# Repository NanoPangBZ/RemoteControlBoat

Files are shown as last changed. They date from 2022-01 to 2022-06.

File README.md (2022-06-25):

# 2022年机创项目(已结束)

## 1、硬件说明(机械创新实验室成员使用船只演示时必看!!!)

	船核心板与船驱动板之间的信号线连接采用MX1.25（4Pin 8Pin都有），虽然驱动板上忘记写标志了，对齐了连接即可。驱动板P3口是给核心板供电（5V）的，核心板的P2、P4是3.3V电源，千万别接5V，不然直接GG!!

    模块接口主要包括MPU6050、nRF24L01和七脚OLED12864，具体连接自己研究吧，这个应该简单。

    **本次比赛中电机等的连接**

    因为船核心板的单片机使用的是自己老项目的拆机芯片，TIM4CH1的出波有些问题，使用PWM模式能出波，但是这个管脚的PWM峰值远远低于3.3V,无法使用这个信号驱动舵机电调等，所以硬件上没有连接！

    因为这个原因，原定使用 TIM4 CH1~CH4 做为电调控制的引脚 **改为** TIM8 CH1~CH4。(注意：驱动板上TIM8口标的是舵机驱动舵机接口，但是软件上并没有使用TIM8控制舵机，而是使用TIM8控制电调。TIM4的CH1和CH4没有使用,CH2和CH3用于控制舵机。)

	主推进无刷电机使用电调控制，电调分别连接TIM8的CH1和CH2，这种电调和其他电调的区别是它用的香蕉头！不要搞错了，另一种电调用来驱动转向电机的，它无法提供主推进无刷电机的电流!!然后主推进电机的电调是可调油门的双向电调，我已经油门行程校准过了，建议看不懂程序就别瞎校准油门行程了！！转向无刷电机的电调它是不可调行程的电调，没有油门行程校准的功能(使用TIM8的CH3和CH4)。

	**遥控器**

	没啥好讲的，Type-C接口有根线忘记连接了，电脑无法识别到CH340就把Type-C翻一面连接。

## 2、软件说明

	自己看代码注释去，懒得BBNN。没学RTOS也能看，底层分的很清除的。

	**boat工程:**

	bsp_pwm.c/.h -> 船核心板输出PWM

	bsp_spi.c/.h -> SPI通讯 用于2.4G通讯模块 和 OLED屏幕 (注意:没有初始化代码)

	bsp_usart.c/.h -> 串口,部分使用的DMA发送,自己看

	bsp_timer.c/.h -> 代码计时器，可用于计算某些代码的运行时长

## 3、写在最后

	没必要老是跟着船走，你可以自己设计一块其它功能的驱动板，调用我的底层去控制其它东西，霍尔啊啥的。驱动板注意做好隔离，别把核心板烧了！！那块板子上的单片机是我自己的！！！！！

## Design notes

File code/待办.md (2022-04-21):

测试遥控器屏幕是否会显示nrf断连消息

购买XT60和香蕉头口

购买水位检测器

购买图传

搭建最终硬件

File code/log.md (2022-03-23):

freeRTOS下通过一个任务函数使用不同的任务参数建立多个任务:

错误示范:



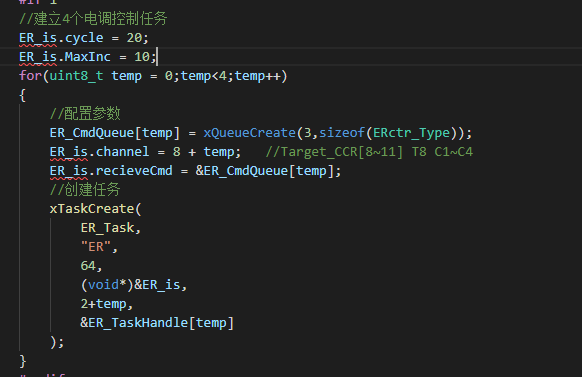
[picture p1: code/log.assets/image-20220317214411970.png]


ER_is->任务参数,函数内定义的局部变量

不能使用同一ER_Type变量建立多个任务,因为TaskCreate函数传入的是地址!相当于多个任务使用了同一个参数

Pass:



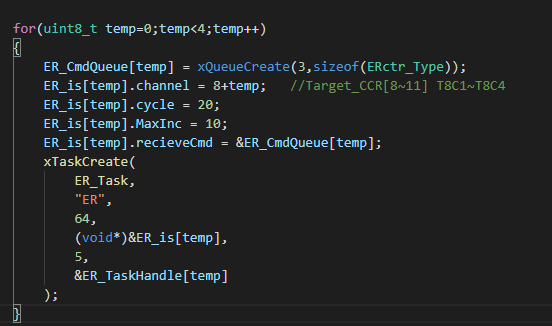
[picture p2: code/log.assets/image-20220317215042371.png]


```c
#include "stdui.g"

void main(void)
{
    
}
```

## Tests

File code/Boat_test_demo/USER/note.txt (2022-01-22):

待办:
    nRF24L01 进入ISR正常
    nRF24L01移植
    6路PWM输出
说明:
-主控芯片待定! 6路PWM(4路50Hz,2路10kHz)、2路PWM捕获、2路ADC采集、1路4Pin-SPI(nRF24L01)、1串口、软件I2C(陀螺仪)
-nrf24l01：只使用P0和P1数据管道。P0用于发送模式下接收ACK信号，P1用于接收模式下接收数据。P0的地址与发射模式下
 发射地址保持一致(发送端P0地址、发送端发射地址和接收端P1地址三者一致)。遥控器发射地址"USER"(5Byte)，P1管道地
 址"BOAT"(5Byte)，船控制器与遥控器相反。

便签:

备注: 2022年机创，水面清洁机器人 船控制器

最后更改日期:2021年1月 庞碧璋 3096470072@qq.com

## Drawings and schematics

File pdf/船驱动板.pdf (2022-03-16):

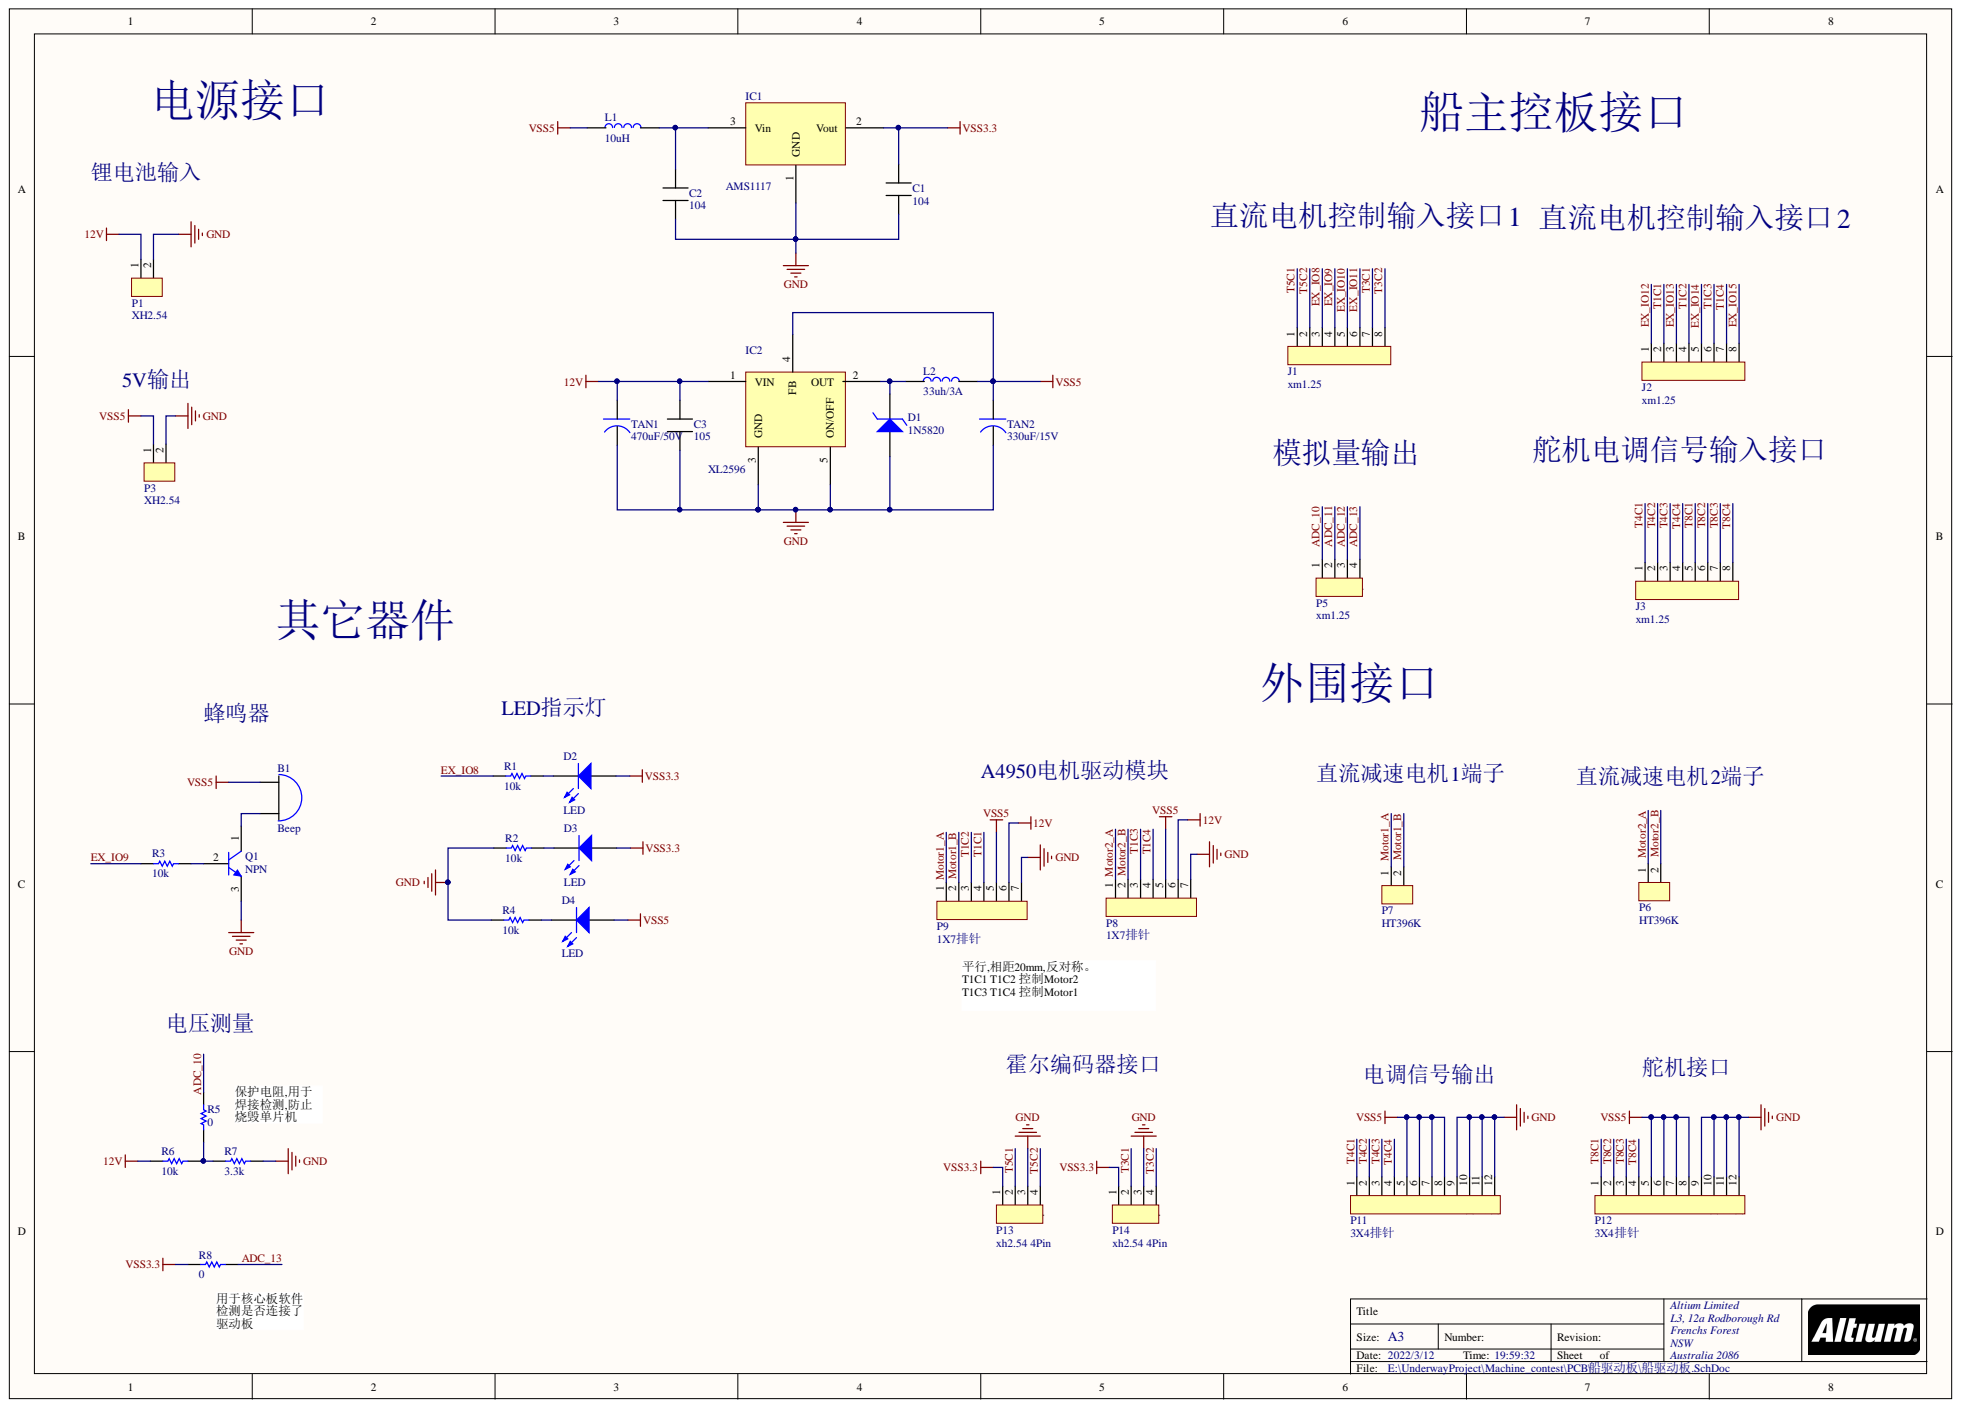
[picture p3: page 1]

Comment | Description | Designator | Footprint | LibRef | Quantity
Beep | | B1 | 蜂鸣器 | Beep | 1
104 | | C1 | C 0603 | 电容 | 1
104 | | C2 | C 0603 | 电容 | 1
105 | | C3 | C 0603 | 电容 | 1
1N5820 | | D1 | 1N5824 | 稳压二极管 | 1
LED | Typical INFRARED GaAs LED D2 | | LED 0603 | LED | 1
LED | Typical INFRARED GaAs LED D3 | | LED 0603 | LED | 1
LED | Typical INFRARED GaAs LED D4 | | LED 0603 | LED | 1
AMS1117 | | IC1 | SOT-223 | AMS1117-3.3 | 1
XL2596 | | IC2 | TO-263-5 | XL2596 | 1
xm1.25 | | J1 | MX1.25 8P LS | 1X8排针 | 1
xm1.25 | | J2 | MX1.25 8P LS | 1X8排针 | 1
xm1.25 | | J3 | MX1.25 8P LS | 1X8排针 | 1
10uH | | L1 | L 0603 | 电感 | 1
33uh/3A | | L2 | CDRH74 | 电感 | 1
XH2.54 | | P1 | XH2.54 2P | 1X2排针 | 1
XH2.54 | | P3 | XH2.54 2P | 1X2排针 | 1
xm1.25 | | P5 | MX1.25 | 1X4排针 | 1
HT396K | | P6 | HT396 - 2P | 1X2排针 | 1
HT396K | | P7 | HT396 - 2P | 1X2排针 | 1
1X7排针 | | P8 | 2.54 1X7Pin | 1X7排针 | 1
1X7排针 | | P9 | 2.54 1X7Pin | 1X7排针 | 1
3X4排针 | | P11 | 2.54 3X4 | 3X4排针 | 1
3X4排针 | | P12 | 2.54 3X4 | 3X4排针 | 1
xh2.54 4Pin | | P13 | XH2.54 -4p | 1X4排针 | 1
xh2.54 4Pin | | P14 | XH2.54 -4p | 1X4排针 | 1
NPN | NPN Bipolar Transistor Q1 | | SOT-23 | NPN | 1
10k | Resistor | R1 | R 0603 | Res | 1
10k | Resistor | R2 | R 0603 | Res | 1
10k | Resistor | R3 | R 0603 | Res | 1
10k | Resistor | R4 | R 0603 | Res | 1
0 | Resistor | R5 | R 0603 | Res | 1
10k | Resistor | R6 | R 0603 | Res | 1
3.3k | Resistor | R7 | R 0603 | Res | 1
0 | Resistor | R8 | R 0603 | Res | 1
470uF/50V | | TAN1 | 10X10.5mm 电解电容极性电容 | | 1
330uF/15V | | TAN2 | 8*10.0mm 电解电容极性电容 | | 1

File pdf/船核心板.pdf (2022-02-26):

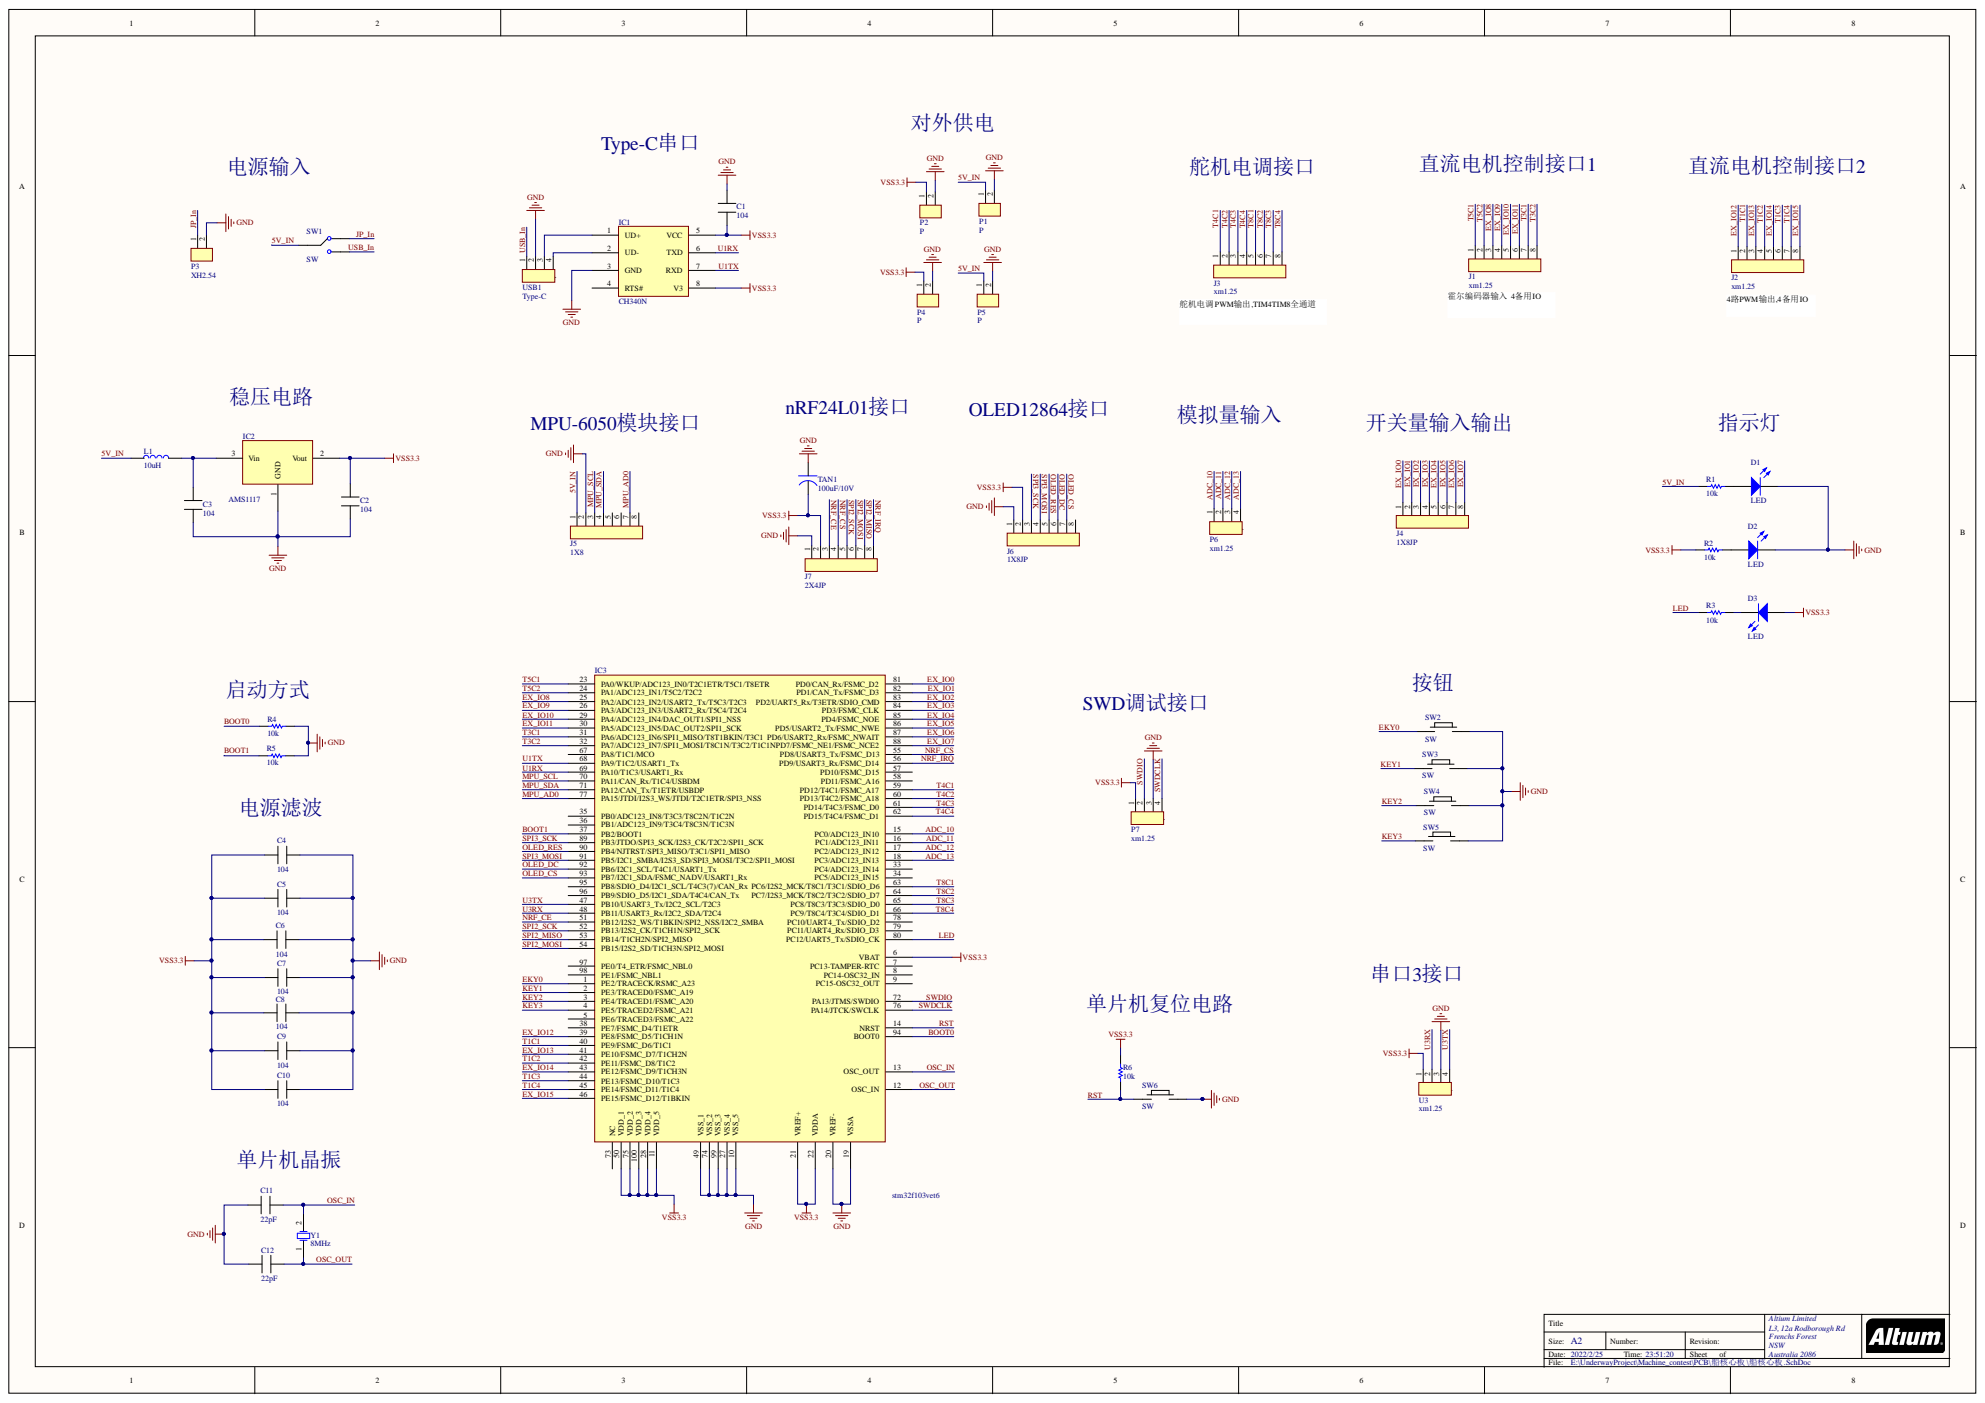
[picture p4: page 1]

GND 3

RTS# 4

Title | Altium Limited L3, 12a Rodborough Rd Frenchs Forest NSW Australia 2086

Size: A2 | Number: | Revision:

Date: 2022/2/25 Time: 23:51:20 | | Sheet of

E:\UnderwayProject\Machine_contest\PCB\船核心板\船核心板.SchDoc

Comment | Description | Designator | Footprint | LibRef | Quantity
104 | | C1, C2, C3, C4, C5, C6, C7, C8, C9, C10 C 0603 | | 电容 | 10
22pF | | C11, C12 | C 0603 | 电容 | 2
LED | Typical INFRARED GaAs LED D1, D2, D3 | | LED 0603 | LED | 3
CH340N | | IC1 | SOP-8 | CH340N | 1
AMS1117 | | IC2 | SOT-223 | AMS1117-3.3 | 1
stm32f103vet6 | | IC3 | LQPF100 12X12 | stm32f103vet6 | 1
xm1.25 | | J1, J2, J3 | MX1.25 8P | 1X8排针 | 3
1X8JP | | J4, J6 | HDR2.54-M-LI-8P | 1X8排针 | 2
1X8 | | J5 | HDR2.54-M-LI-8P | 1X8排针 | 1
2X4JP | | J7 | HDR2.54-LI-2x4P | 1X8排针 | 1
10uH | | L1 | L 0603 | 电感 | 1
P | | P1, P2, P4, P5 | XH2.54 2P | 1X2排针 | 4
XH2.54 | | P3 | XH2.54 2P | 1X2排针 | 1
xm1.25 | | P6, P7 | MX1.25 | 1X4排针 | 2
10k | Resistor | R1, R2, R3, R4, R5, R6R 0603 | | Res | 6
SW | | SW1 | 拨动开关 9X3.5X3.5 侧卧 单刀双置开关 | | 1
SW | | SW2, SW3, SW4, SW5, SW6 SW SMD 3x6x2.5 | | 弹簧开关 | 5
100uF/10V | | TAN1 | 6.3*5.4mm 电解电容极性电容 | | 1
xm1.25 | | U3 | 2.54 _ 4Pin | 1X4排针 | 1
Type-C | | USB1 | USB Type-C | 1X4排针 | 1
8MHz | Crystal Oscillator | Y1 | OSC SMD | 晶振 | 1

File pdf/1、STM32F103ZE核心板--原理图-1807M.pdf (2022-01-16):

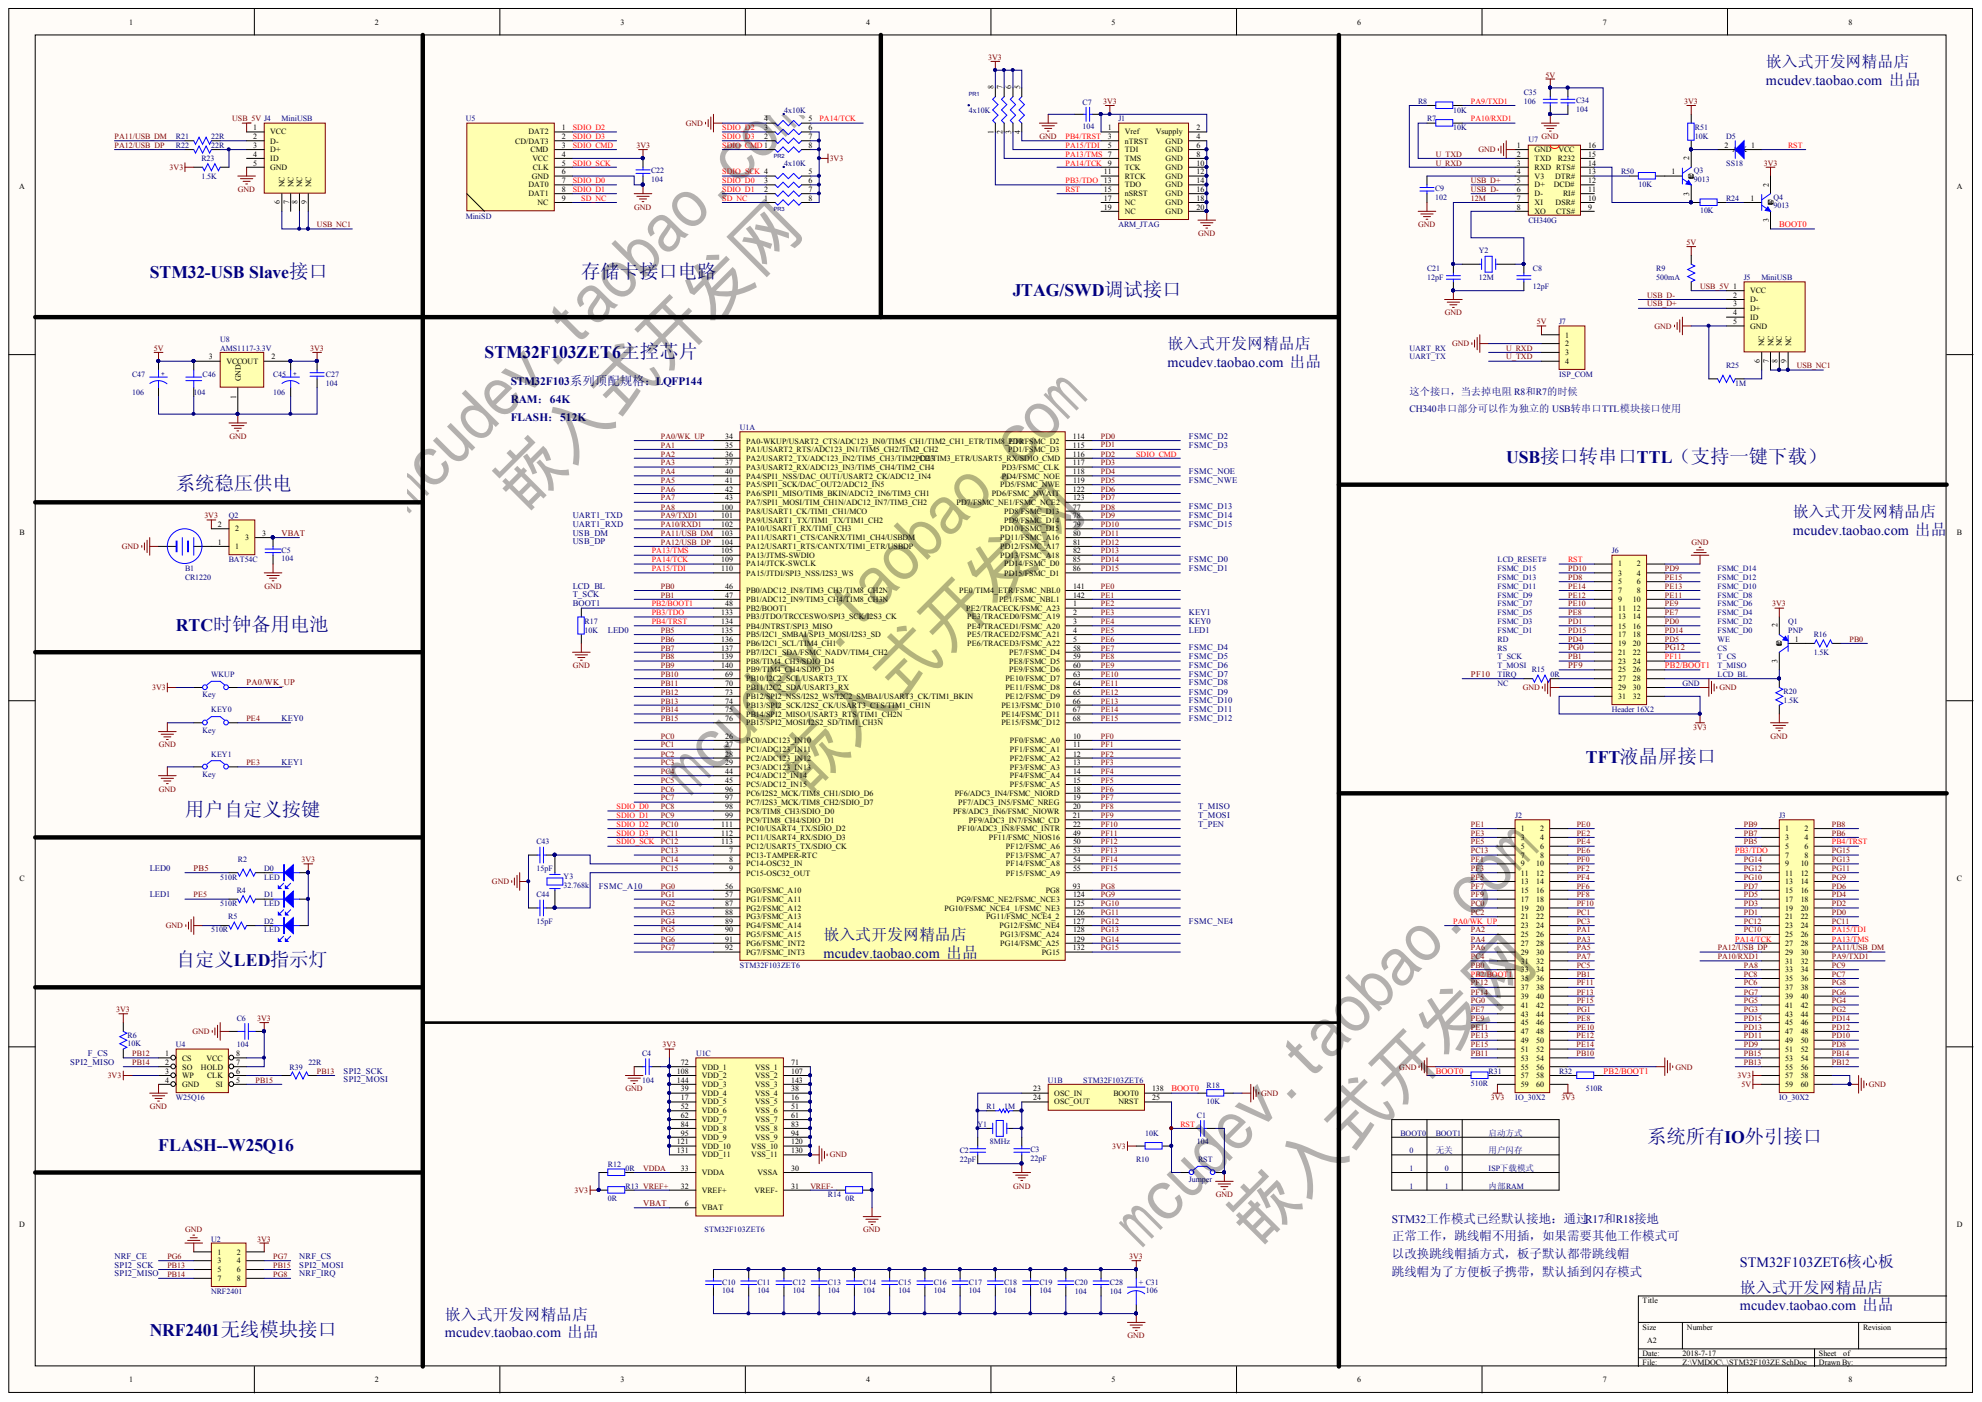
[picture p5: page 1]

STM32F103ZET6核心板 mcudev.taobao.com 出品

嵌入式开发网精品店
mcudev.taobao.com 出品

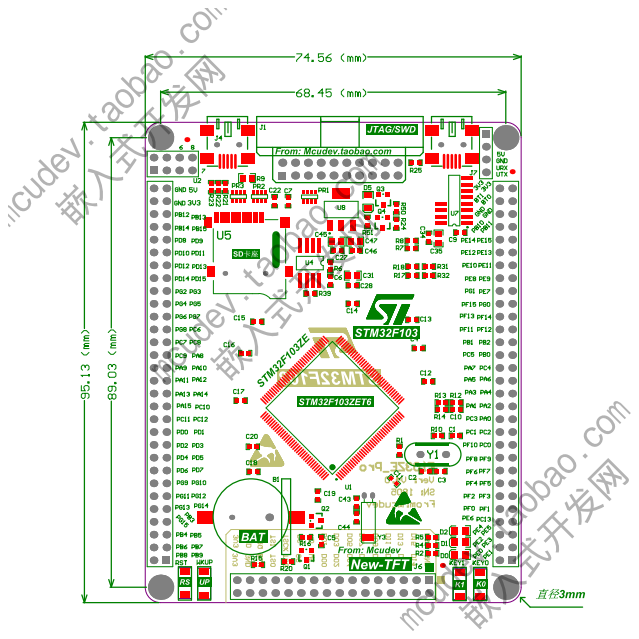
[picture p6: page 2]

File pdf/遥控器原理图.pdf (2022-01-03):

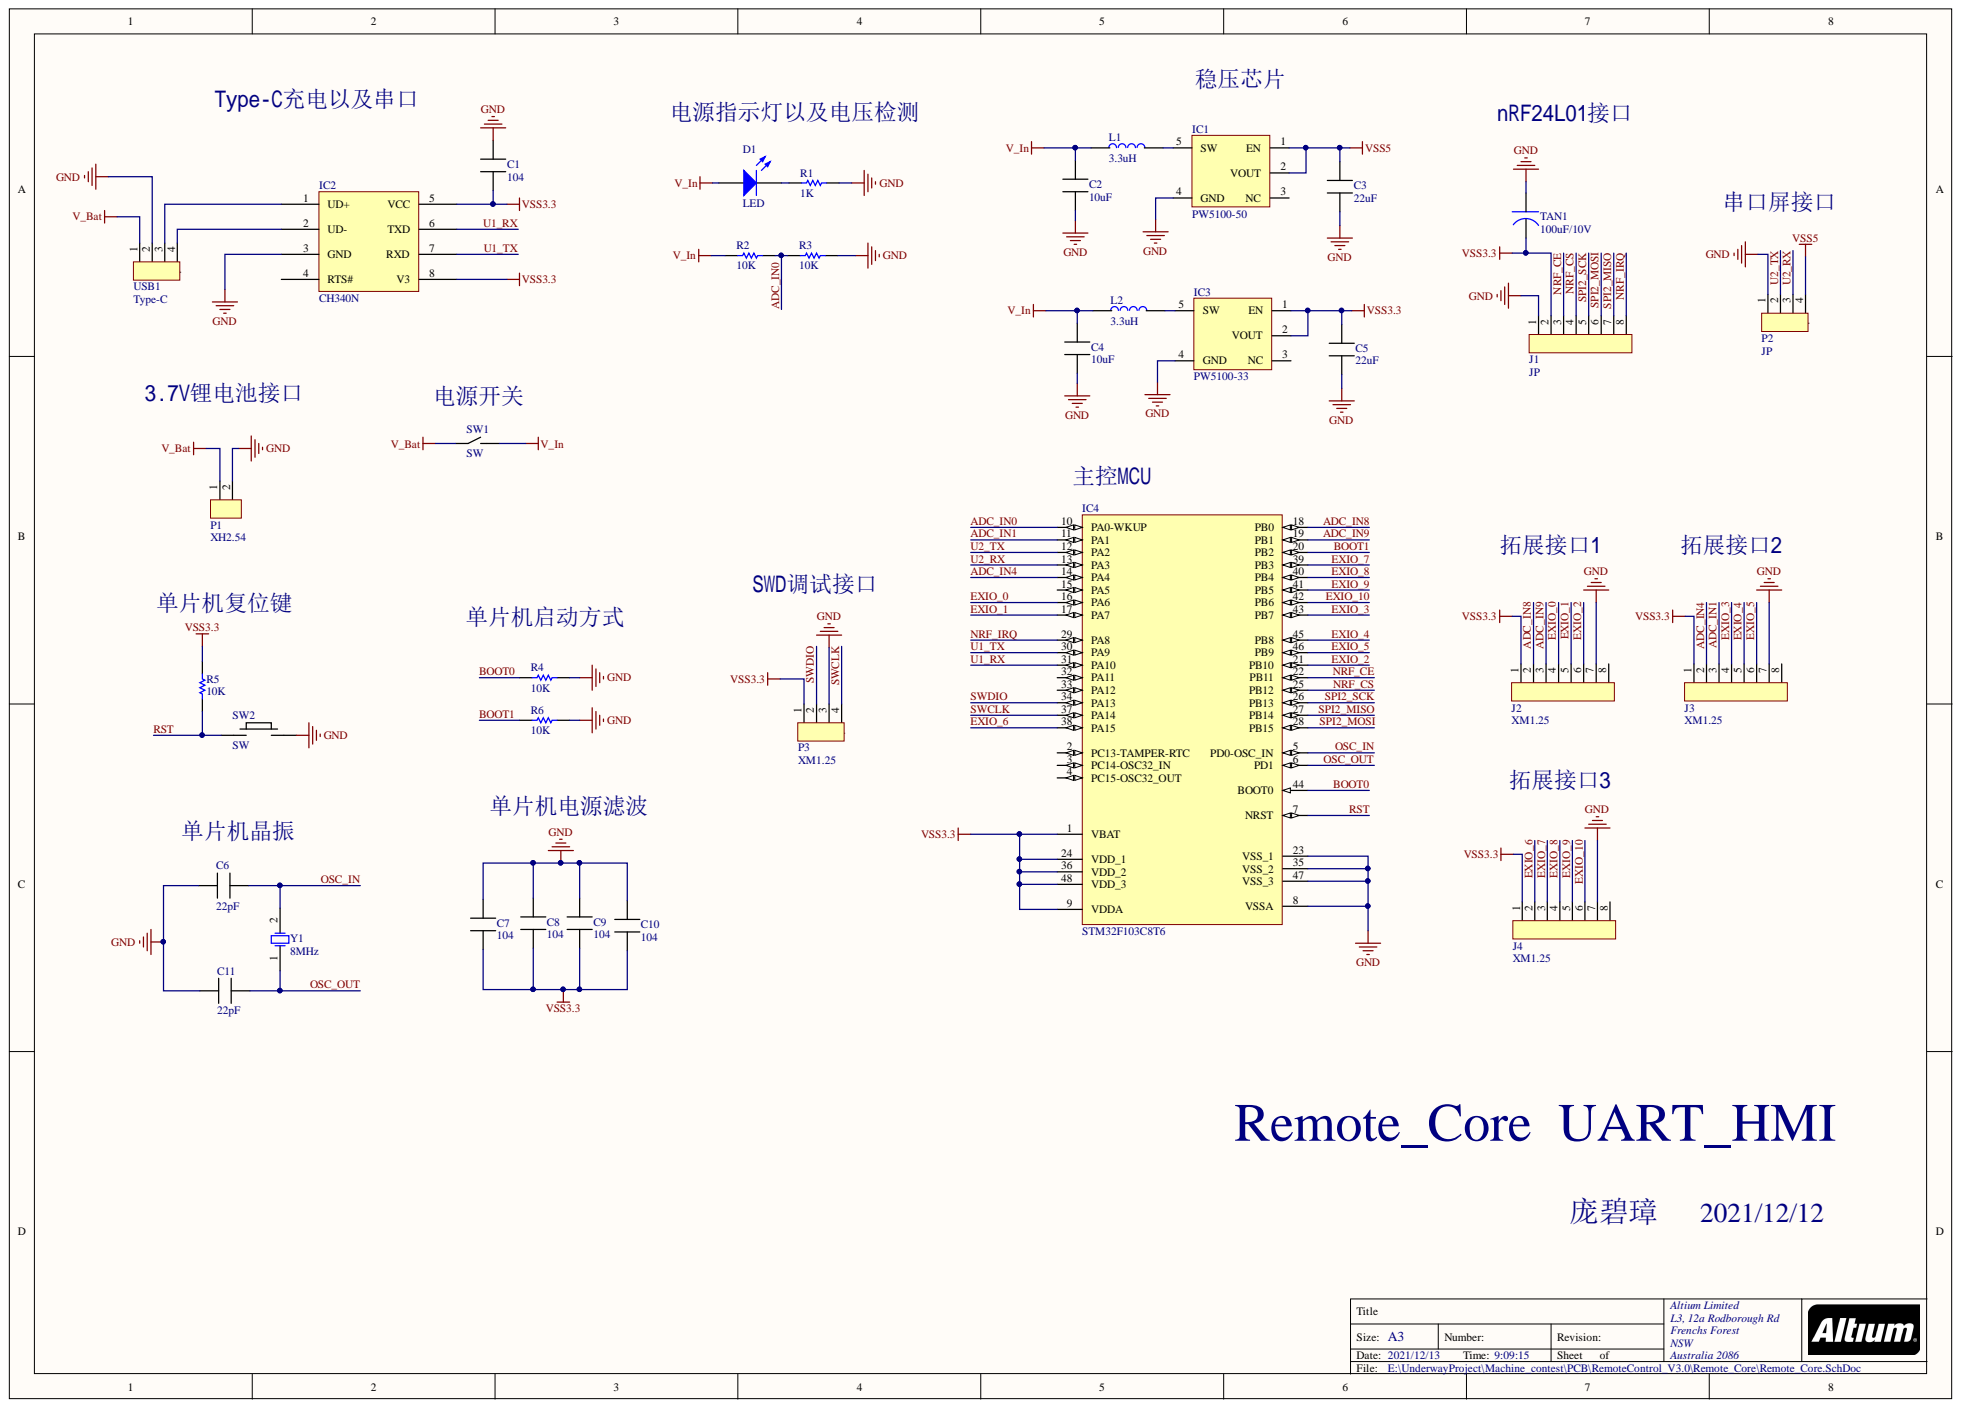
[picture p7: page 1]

Ti t l e | A l t ium Li m i ted L3, 12a Rodborough R d F renchs Fores t NSW Aus t ral ia 2086

Size: A 3 | Number : | Revi s ion:
Date: 2021/12/13 Ti me: 9:09:15 | | Sheet of

Comment | Description | Designator | Footprint | LibRef | Quantity
104 | | C1 | C 0603 | 电容 | 1
10uF | | C2 | C 0603 | 电容 | 1
22uF | | C3 | C 0603 | 电容 | 1
10uF | | C4 | C 0603 | 电容 | 1
22uF | | C5 | C 0603 | 电容 | 1
22pF | | C6 | C 0603 | 电容 | 1
104 | | C7 | C 0603 | 电容 | 1
104 | | C8 | C 0603 | 电容 | 1
104 | | C9 | C 0603 | 电容 | 1
104 | | C10 | C 0603 | 电容 | 1
22pF | | C11 | C 0603 | 电容 | 1
LED | Typical INFRARED GaAs LED D1 | | LED 0603 | LED | 1
PW5100-50 | | IC1 | PW5100 | PW5100 | 1
CH340N | | IC2 | SOP-8 | CH340N | 1
PW5100-33 | | IC3 | PW5100 | PW5100 | 1
STM32F103C8T6 | | IC4 | LQPF48 7X7 | stm32f103c8t6 | 1
JP | | J1 | HDR2.54-LI-2x4P | 1X8排针 | 1
XM1.25 | | J2 | MX1.25 8P | 1X8排针 | 1
XM1.25 | | J3 | MX1.25 8P | 1X8排针 | 1
XM1.25 | | J4 | MX1.25 8P | 1X8排针 | 1
3.3uH | | L1 | 630 | 电感 | 1
3.3uH | | L2 | 630 | 电感 | 1
XH2.54 | | P1 | XH2.54 2P | 1X2排针 | 1
JP | | P2 | 2.54 _ 4Pin | 1X4排针 | 1
XM1.25 | | P3 | MX1.25 | 1X4排针 | 1
1K | Resistor | R1 | R 0603 | Res | 1
10K | Resistor | R2 | R 0603 | Res | 1
10K | Resistor | R3 | R 0603 | Res | 1
10K | Resistor | R4 | R 0603 | Res | 1
10K | Resistor | R5 | R 0603 | Res | 1
10K | Resistor | R6 | R 0603 | Res | 1
SW | | SW1 | 拨动开关 9X3.5X3.5 侧卧 开关 | | 1
SW | | SW2 | SW SMD 3x6x2.5 | 弹簧开关 | 1
100uF/10V | | TAN1 | 6.3*5.4mm 电解电容极性电容 | | 1
Type-C | | USB1 | USB Type-C | 1X4排针 | 1
8MHz | Crystal Oscillator | Y1 | OSC SMD | 晶振 | 1

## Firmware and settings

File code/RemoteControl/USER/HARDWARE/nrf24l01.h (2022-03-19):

#ifndef _NRF24L01_H_
#define _NRF24L01_H_

#include "self_stm32f10x.h"

/*************************************************
 * nrf24l01的驱动
 * nrf24l01.c
 * nrf24l01.h
 * nrf24l01_micro.h <- nrf寄存器地址
 * 
 * 功能:
 * 驱动nrf24l01 1对1 半双工通讯 (只支持静态接收字节长度,长度可配置)
 * 可使用文件内部的sbuffer来缓存多次接收(可通过宏配置)
 * 
 * 若宏NRF24_USE_SBUFFER==1,nRF24L01_InterruptHandle()会
 * 将nrf RxFIFO中的值读入到nRF24L01_Sbuffer中
 * 若宏NRF24_USE_BUF_LEN==0,则nRF24L01_Sbuffer会被下次接收时
 * 调用nRF24L01_InterruptHandle()覆盖
 * 
 * 关于移植:
 * 
 * 实现nrf24l01.c中的宏和nrf_support_init()
 * 注意!nrf的中断服务函数没有写接口,可以在外部
 * 的中断函数中调用nRF24L01_InterruptHandle()
 * 
 * 如果是接收中断可能会耗费较长的时序,不建议直接
 * 在中断服务函数中调用nRF24L01_InterruptHandle()
 * 
 * 如果不想使用外部中断,可以不在nrf_support_init()
 * 中配置中断,轮询nRF24L01_InterruptHandle()即可
 * 
 * 作者: 庞碧璋
 * Github: https://github.com/CodingBugStd
 * csdn:   https://blog.csdn.net/RampagePBZ
 * Encoding: utf-8
 * 最后更改时间: 2022/2/14
*************************************************/

/*************************自定义宏**********************************/
// spi_port
#define  NRF24L01_SPIx                SPI2                  // SPI 端口   

// 第3脚:CE
#define  NRF24L01_CE_GPIO             GPIOB                 // CE 工作模式开启， 高电平有效，发射/接收模式控制
#define  NRF24L01_CE_PIN              GPIO_Pin_11
// 第4脚:CSN
#define  NRF24L01_CSN_GPIO            GPIOB                 // SPI 软件片选线
#define  NRF24L01_CSN_PIN             GPIO_Pin_12
// 第5脚:SCK
#define  NRF24L01_SCK_GPIO            GPIOB                 // SPI SCK
#define  NRF24L01_SCK_PIN             GPIO_Pin_13
// 第65脚:MOSI
#define  NRF24L01_MOSI_GPIO           GPIOB                 // SPI MOSI
#define  NRF24L01_MOSI_PIN            GPIO_Pin_15
// 第7脚:MISO
#define  NRF24L01_MISO_GPIO           GPIOB                 // SPI MISO
#define  NRF24L01_MISO_PIN            GPIO_Pin_14
// 第8脚:IRQ
#define  NRF24L01_IQR_GPIO           GPIOA                 // SPI IRQ
#define  NRF24L01_IQR_PIN            GPIO_Pin_8
#define  NRF24L01_IQR_Channel        EXTI9_5_IRQn
#define  NRF24L01_IQR_SourceGPIO    GPIO_PortSourceGPIOA
#define  NRF24L01_IQR_PinSource     GPIO_PinSource8
#define  NRF24L01_IQR_Line          EXTI_Line8

#define NRF24L01_CE     0
#define NRF24L01_CS     1
#define NRF24L01_MOSI   2
#define NRF24L01_MISO   3
#define NRF24L01_SCK    4

/*************************************功能配置宏************************************************/

//相关配置
//nRF24初始化的默认配置
#define DEFAULT_TxAddr  "USER"
#define DEFAULT_RxAddr  "BOAT"
#define DEFAULT_Channel 0       //2400MHz频段
#define DEFAULT_RETRY   2       //最大自动重发次数
#define DEFAULT_RETRY_CYCLE 1   //重发间隔 单位:250us
#define DEFAULT_Rx_Length   32  //默认StaticPayload长度
//其它配置
#define NRF24_BUF_MAXLEN    64  //缓存区长度,NRF24_USE_BUF_LEN!=0 时才有用
#define NRF24_USE_BUF_LEN   0   //非0:缓存区第一字节用于表示缓存区长度,使能这个宏可以缓存nrf24的多次接收
#define NRF24_USE_SBUFFER   1   //非0:接收中断时将RxFIFO的值载入内部缓存nRF24L01_Sbuffer中,若NRF24_USE_BUF_LEN=0则会覆盖上次接收!

#if NRF24_USE_BUF_LEN
//缓存区第一字节表示缓存区当前长度
static uint8_t nRF24L01_Sbuffer[NRF24_BUF_MAXLEN+1] = {0};
#elif NRF24_USE_SBUFFER
static uint8_t nRF24L01_Sbuffer[32] = {0};
#endif

typedef struct
{
    uint8_t Channel;    //频道  0~125 -> 1MHz + 2.4G
    uint8_t retry;      //自动重发次数 最大16
    uint8_t retry_cycle;//自动重发时间间隔 250us单位 最大16(4000us)
    uint8_t Rx_Length;  //静态接收长度
    uint8_t RX_Addr[5]; //接收地址    ->  发射方地址
    uint8_t TX_Addr[5]; //发射方地址  ->  目标接收地址
}nRF24L01_Cfg;

static nRF24L01_Cfg CurrentCfg;     //当前nRF24L01的配置

/*************************************函数************************************************/

//底层函数

uint8_t nRF24L01_Send_Cmd(uint8_t cmd);
uint8_t nRF24L01_Send_CmdAndData(uint8_t cmd,uint8_t*buf,uint8_t len);
uint8_t nRF24L01_Read_Reg(uint8_t addr);
uint8_t nRF24L01_Read_Buf(uint8_t addr,uint8_t*buf,uint8_t len);
uint8_t nRF24L01_Write_Reg(uint8_t addr,uint8_t dat);
uint8_t nRF24L01_Write_Buf(uint8_t addr,uint8_t*buf,uint8_t len);

//用户函数

uint8_t nRF24L01_Init(void);
uint8_t nRF24L01_Check(void);
uint8_t nRF24L01_Status(void);
uint8_t nRF24L01_Config(nRF24L01_Cfg*Cfg);
uint8_t nRF24L01_Send(uint8_t*buf,uint8_t len);
uint8_t nRF24L01_Read_RxFIFO(uint8_t*buf);
uint8_t nRF24L01_Rx_Mode(void);
#if NRF24_USE_SBUFFER
uint8_t nRF24L01_Read_RxSbuffer(uint8_t*buf,uint8_t len);
uint8_t*nRF24L01_Get_RxBufAddr(void);
uint8_t*nRF24L01_FIFO_To_Sbuffer(void);
#if NRF24_USE_BUF_LEN
uint8_t nRF24L01_Read_SbufferLen(void);
void nRF24L01_Push_Sbuffer(uint8_t len);
void nRF24L01_Clear_Sbuffer(void);
#endif  //NRF24_USE_BUF_LEN
#endif //NRF24_USE_SBUFFER

void nRF24L01_InterruptHandle(void);
void Rx_Handler(void);   //接收中断
void NoACK_Handle(void); //未应答中断
void Tx_Handle(void);    //发送完成中断

#endif

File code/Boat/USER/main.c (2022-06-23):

#include "main.h"

#pragma	diag_suppress	870	//屏蔽汉字警告

//nRF24L01初始化结构体
nRF24L01_Cfg nRF24_Cfg;
static uint8_t RxAddr[5] = {0x43,0x16,'R','C',0xFF};	//遥控器地址
static uint8_t TxAddr[5] = {0x43,0x16,'B','T',0xFF};	//船地址

//任务参数
uint8_t main_fre = 50;				//主任务频率
uint8_t oled_fre = 20;				//OLED刷新频率
uint8_t WaterLine_fre = 50;			//水位测量频率
uint8_t nrf_maxDelay = 200;			//nrf最大超时时间
uint8_t mpu_fre = DEFAULT_MPU_HZ;	//mpu更新频率
ER_Type	ER_is[4];					//电调任务参数
DCMotor_Type DCMotor_is[2];			//直流电机任务参数
StreetMotor_Type STMotor_is[3];		//舵机任务参数

//任务句柄
TaskHandle_t	RTOSCreateTask_TaskHandle = NULL;	//创建任务句柄
TaskHandle_t	ReplyMaster_TaskHandle = NULL;		//主机回复任务句柄
TaskHandle_t	OLED_TaskHandle = NULL;				//oled刷新任务句柄
TaskHandle_t	nRF24L01_Intterrupt_TaskHandle = NULL;	//nrf中断任务句柄
TaskHandle_t	MPU_TaskHandle = NULL;				//陀螺仪刷新任务句柄
TaskHandle_t	KeyInput_TaskHandle = NULL;			//按键任务句柄
TaskHandle_t	Voltage_TaskHandle = NULL;			//电池电压检测任务句柄
TaskHandle_t	DepthSensor_TaskHandle = NULL;		//水位深度检测任务句柄
TaskHandle_t	Beep_TaskHandle = NULL;				//蜂鸣器任务句柄
TaskHandle_t	ER_TaskHandle[4] = {NULL,NULL,NULL,NULL};	//电调任务句柄
TaskHandle_t	DCMotor_TaskHandle[2] = {NULL,NULL};		//直流电机控制任务句柄
TaskHandle_t	StreetMotor_TaskHandle[4] = {NULL,NULL,NULL,NULL};	//舵机任务句柄

//队列句柄
SemaphoreHandle_t	nRF24_ISRFlag = NULL;		//nrf24硬件中断标志
SemaphoreHandle_t	nRF24_RecieveFlag = NULL;	//nrf24接收标志(数据已经进入单片机,等待处理)
QueueHandle_t		nRF24_SendResult = NULL;	//nrf24发送结果
QueueHandle_t		wait_handle_receive = NULL;	//等待处理的接收信息
QueueHandle_t		ER_CmdQueue[4] = {NULL,NULL,NULL,NULL};	//电调任务命令接收队列
QueueHandle_t		DCMotor_CmdQueue[2] = {NULL,NULL};		//直流电机任务命令接收队列
QueueHandle_t		STMotor_CmdQueue[4] = {NULL,NULL,NULL,NULL};	//舵机任务命令接收队列
QueueHandle_t		Beep_CmdQueue = NULL;		//蜂鸣器命令队列
SemaphoreHandle_t	mpuDat_occFlag = NULL;		//mpu数据占用标志(互斥信号量)
SemaphoreHandle_t	sysStatus_occFlag = NULL;	//系统状态变量占用标志(互斥信号量)

//全局变量
float mpu_data[3] = {0,0,0};    //姿态 -> mpuDat_occFlag保护
float BatVol = 0.0f;			//电池电压
float Depth = 0.0f;				//吃水深度
sysStatus_Type sysStatus;       //系统状态 -> sysStatus_occFlag保护
PID_Handle	Yaw_pid_Handle;		//航向角pid

void RTOSCreateTask_Task(void*ptr);		//初始化任务
void Er_Cal(void);	//油门行程校准

int main(void)
{
	uint8_t nrf_err;
	uint8_t mpu_err;

	NVIC_PriorityGroupConfig(NVIC_PriorityGroup_4);
	//关闭JATG调试接口,开启SWD调试接口
	RCC_APB2PeriphClockCmd(RCC_APB2Periph_AFIO,ENABLE);
	GPIO_PinRemapConfig(GPIO_Remap_SWJ_JTAGDisable,ENABLE);

	BSP_PWM_Init();
	BSP_LED_Init();
	BSP_Usart_Init();
	//BSP_Timer_Init();
	BSP_Key_Init();
	BSP_Beep_Init();
	BSP_ADC_Init();
	BSP_i2c_Init();

	//OLED初始化 -> 需要SPI
	OLED12864_Init();
	OLED12864_Show_String(0,0,"hardware init",1);
	OLED12864_Refresh();


	Er_Cal();	//油门行程校准

	//MPU初始化	-> 需要IIC
	mpu_err = MPU_Init();
	if(mpu_err)
	{
		OLED12864_Show_String(2,0,"mpu err",1);
	}else
	{
		OLED12864_Show_String(2,0,"mpu pass",1);
		if(mpu_dmp_init())	//初始化官方的DMP固件库
			OLED12864_Show_String(3,0,"6050 dmp err",1);
	}

	//nrf24初始化和配置 -> 需要SPI
	nrf_err = nRF24L01_Init();
	if(nrf_err)	//检查硬件
	{
		OLED12864_Show_String(1,0,"nrf err.restarting",1);
		OLED12864_Refresh();
		while(nrf_err == 1)
		{
			nrf_err = nRF24L01_Init();
			soft_delay_ms(100);
		}
	}

	//nRF24L01 相关配置
	nRF24_Cfg.Channel = 50;	//2.45GHz 通讯频段
	nRF24_Cfg.retry = 10;	//最大重发次数
	nRF24_Cfg.retry_cycle = 1;	//重发周期
	nRF24_Cfg.Rx_Length = 32;	//结束长度
	MemCopy(TxAddr,nRF24_Cfg.TX_Addr,5);
	MemCopy(RxAddr,nRF24_Cfg.RX_Addr,5);
	nRF24L01_Config(&nRF24_Cfg);	//配置nRF24L01
	nRF24L01_Rx_Mode();

	OLED12864_Clear_Page(1);
	OLED12864_Show_String(1,0,"nrf pass",1);
	OLED12864_Refresh();

	//创建RTOS初始化任务
	if(nrf_err == 0 & mpu_err == 0)
	{
		xTaskCreate(
			RTOSCreateTask_Task,
			"init",
			256,
			NULL,
			15,
			&RTOSCreateTask_TaskHandle
		);
	}

	vTaskStartScheduler();

	while(1);
}

void RTOSCreateTask_Task(void*ptr)
{
	//系统状态sysStatus
    sysStatus.nrf_signal = 0;
	//建立 队列 信号量
    nRF24_ISRFlag = xSemaphoreCreateBinary();		//nrf外部中断标志,由isr给出
	nRF24_RecieveFlag = xSemaphoreCreateBinary();	//nrf发生接收中断标志
	nRF24_SendResult = xQueueCreate(1,1);			//nrf发送结果标志
    mpuDat_occFlag = xSemaphoreCreateMutex();		//mpu_data[3] 保护
    sysStatus_occFlag = xSemaphoreCreateMutex();	//sysStatus 保护
	Beep_CmdQueue = xQueueCreate(3,sizeof(BeepCtr_Type));
	//建立2个舵机控制任务
	STMotor_CmdQueue[0] = xQueueCreate(3,sizeof(StreetMotorCtr_Type));
	STMotor_is[0].queueAddr = &STMotor_CmdQueue[0];
	STMotor_is[0].streetMotor = streetMotor[0];	//见hardware_def.h
	STMotor_is[0].cycle = 40;	//25Hz执行频率
	STMotor_is[0].angle_inc = 4.7f;
	xTaskCreate(
		StreetMotor_Task,
		"SM",
		72,
		(void*)&STMotor_is[0],
		6,
		&StreetMotor_TaskHandle[0]
	);
	STMotor_CmdQueue[1] = xQueueCreate(3,sizeof(StreetMotorCtr_Type));
	STMotor_is[1].queueAddr = &STMotor_CmdQueue[1];
	STMotor_is[1].streetMotor = streetMotor[1];	//见hardware_def.h
	STMotor_is[1].cycle = 40;	//25Hz执行频率
	STMotor_is[1].angle_inc = 7.0;
	xTaskCreate(
		StreetMotor_Task,
		"SM",
		
		72,
		(void*)&STMotor_is[1],
		6,
		&StreetMotor_TaskHandle[1]
	);
	//建立2个直流电机控制任务
	for(uint8_t temp=0;temp<2;temp++)
	{
		DCMotor_CmdQueue[temp] = xQueueCreate(3,sizeof(DCMotorCtr_Type));	//创建命令接收队列
		DCMotor_is[temp].queueAddr = &DCMotor_CmdQueue[temp];				//设置命令接收队列地址
		DCMotor_is[temp].cycle = 20;	//50Hz执行频率
		DCMotor_is[temp].max_inc = 10;
		DCMotor_is[temp].a4950 = a4950[temp];	//见hardware_def.h
		xTaskCreate(
			Motor_Task,
			"MT",
			64,
			(void*)&DCMotor_is[temp],
			5,
			&DCMotor_TaskHandle[temp]
		);
	}
	//建立4个电调控制任务
	for(uint8_t temp=0;temp<4;temp++)
	{
		ER_CmdQueue[temp] = xQueueCreate(3,sizeof(ERctr_Type));		//创建命令接收队列
		ER_is[temp].queueAddr = &ER_CmdQueue[temp];					//设置命令接收队列地址
		ER_is[temp].er = er[temp];	//见hardware_def.h
		ER_is[temp].cycle = 20;
		ER_is[temp].max_inc = 20;
		xTaskCreate(
        	ER_Task,
        	"ER",
        	72,
        	(void*)&ER_is[temp],
        	5,
        	&ER_TaskHandle[temp]
    	);
	}
	#if 1
	//建立nrf回复主机任务
    xTaskCreate(
        ReplyMaster_Task,
        "Reply",
        256,
        (void*)&nrf_maxDelay,
        11,
        &ReplyMaster_TaskHandle
    );
	#endif
	//建立陀螺仪任务
    xTaskCreate(
        MPU_Task,
        "mpu",
        256,
        (void*)&mpu_fre,
        10,
        &MPU_TaskHandle
    );
	#if 1
	//建立oled显示任务
    xTaskCreate(
        OLED_Task,
        "oled",
        256,
        (void*)&oled_fre,
        8,
        &OLED_TaskHandle
    );
	#endif
	//建立nrf中断处理任务
    xTaskCreate(
        nRF24L01_Intterrupt_Task,
        "nrf interrupt",
        128,
        NULL,
        14,
        &nRF24L01_Intterrupt_TaskHandle
    );
	//建立水位检测任务
    xTaskCreate(
        DepthSensor_Task,
        "depth",
        48,
        &WaterLine_fre,
        9,
        &Voltage_TaskHandle
    );
	//建立电池电压检测任务
    xTaskCreate(
        Voltage_Task,
        "batvol",
        48,
        NULL,
        3,
        &Voltage_TaskHandle
    );
	//建立按键输入任务
    xTaskCreate(
        KeyInput_Task,
        "key",
        64,
        NULL,
        7,
        &KeyInput_TaskHandle
    );
	//建立蜂鸣器任务
	xTaskCreate(
		Beep_Task,
		"Beep",
		48,
		NULL,
		2,
		&Beep_TaskHandle
	);
	//鸣响,表示开始运行
	Beep_ON(Mu_Fre[4]);
	soft_delay_ms(800);
	Beep_OFF();
	//删除自身
    vTaskDelete(NULL);
}

//油门校准
void Er_Cal(void)
{
	//油门行程校准
	if(Key_Read(0) == Key_Press)
	{
		OLED12864_Show_String(0,0,"calibration",1);
		OLED12864_Refresh();
		soft_delay_ms(2000);
		ER_UndirOut(&er[0],0);
		ER_UndirOut(&er[1],0);
		ER_UndirOut(&er[2],0);
		ER_UndirOut(&er[3],0);
		while(Key_Read(0) != Key_Press);
		OLED12864_Show_String(1,0,"Set Max",1);
		OLED12864_Refresh();
		ER_UndirOut(&er[0],500);
		ER_UndirOut(&er[1],500);
		ER_UndirOut(&er[2],500);
		ER_UndirOut(&er[3],500);
		soft_delay_ms(300);
		while(Key_Read(0) != Key_Press);
		OLED12864_Show_String(1,0,"Set Med",1);
		OLED12864_Refresh();
		ER_UndirOut(&er[0],0);
		ER_UndirOut(&er[1],0);
		ER_UndirOut(&er[2],0);
		ER_UndirOut(&er[3],0);
		soft_delay_ms(300);
	}
}

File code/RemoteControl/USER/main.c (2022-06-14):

#include "main.h"

#pragma	diag_suppress	870	//屏蔽汉字警告

//nRF24L01初始化结构体
nRF24L01_Cfg nRF24_Cfg;
static uint8_t TxAddr[5] = {0x43,0x16,'R','C',0xFF};	//遥控器地址
static uint8_t RxAddr[5] = {0x43,0x16,'B','T',0xFF};	//船地址

//任务参数
uint8_t SendFre = 50;	//nrf24通讯频率
uint8_t RockerFre = 25;	//摇杆采样频率
uint8_t HMI_Fre = 24;	//串口屏幕刷新频率
uint8_t Key_Fre = 10;	//按钮扫描频率

//任务句柄
TaskHandle_t RTOS_CreatTask_TaskHandle = NULL;
TaskHandle_t RemoteControl_TaskHandle = NULL;
TaskHandle_t nRF24L01_Intterrupt_TaskHandle = NULL;
TaskHandle_t User_FeedBack_TaskHandle = NULL;
TaskHandle_t Rocker_TaskHandle = NULL;
TaskHandle_t HMI_TaskHandle = NULL;
TaskHandle_t KeyInput_TaskHandle = NULL;
TaskHandle_t HMI_UpDataHandle = NULL;

//队列句柄
SemaphoreHandle_t	nRF24_ISRFlag = NULL;		//nrf24硬件中断标志
SemaphoreHandle_t	nRF24_RecieveFlag = NULL;	//nrf24接收标志(数据已经进入单片机,等待处理)
QueueHandle_t		nRF24_SendResult = NULL;	//nrf24发送结果
SemaphoreHandle_t	boatGyroscope_occFlag = NULL;		//船只姿态数据占用标志(互斥信号量)

//全局变量
uint8_t nrf_signal = 0;		//nrf信号强度 0~10
float Depth = 0.0f;			//深度 单位cm
float BoatGyroscope[3];			//船只返回的姿态 boatGyroscope_occFlag保护
float BoatVoltage;
uint8_t rockerInput[4];			//摇杆输入
uint8_t SwitchValue = 0;	//开关量 8开关

void RTOS_CreatTask_Task(void*ptr);

int main(void)
{
	uint8_t nrf_err;

	//中断优先级分组 4位主优先级 0位子优先级
	NVIC_PriorityGroupConfig(NVIC_PriorityGroup_4);
	//关闭JTAG调试接口
	RCC_APB2PeriphClockCmd(RCC_APB2Periph_AFIO,ENABLE);
	GPIO_PinRemapConfig(GPIO_Remap_SWJ_JTAGDisable,ENABLE);

	//串口初始化
	BSP_Usart_Init();
	BSP_ADC_Init();	//ADC初始化
	BSP_LED_Init();
	BSP_Key_Init();

	//串口屏初始化
	soft_delay_ms(500);
	//串口屏开机要一段时间
	//为了串口屏能完整的接收到复位数据
	//初始化两次
	HMI_Reset();
	HMI_Reset();
	soft_delay_ms(500);

	//nRF24L01初始化
	nrf_err = nRF24L01_Init();
	if(nrf_err)
	{
		HMI_Msg("nrf err");
	}else
	{
		//nRF24L01 相关配置
		nRF24_Cfg.Channel = 50;	//2.45GHz 通讯频段
		nRF24_Cfg.retry = 10;	//最大重发次数
		nRF24_Cfg.retry_cycle = 1;	//重发周期
		nRF24_Cfg.Rx_Length = 32;	//结束长度
		MemCopy(TxAddr,nRF24_Cfg.TX_Addr,5);
		MemCopy(RxAddr,nRF24_Cfg.RX_Addr,5);
		nRF24L01_Config(&nRF24_Cfg);	//配置nRF24L01	
		HMI_Msg("nrf pass");
		nRF24L01_Rx_Mode();
	}

	soft_delay_ms(1000);

	xTaskCreate(
		RTOS_CreatTask_Task,
		"CreatTask",
		144,
		NULL,
		15,
		&RTOS_CreatTask_TaskHandle
	);

	vTaskStartScheduler();
	while(1);
}

void RTOS_CreatTask_Task(void*ptr)
{
    nRF24_ISRFlag = xSemaphoreCreateBinary();		//创建nrf中断信号量 -> 由单片机(硬件)外部中断给出
	nRF24_RecieveFlag = xSemaphoreCreateBinary();	//创建nrf接收中断信号量 -> 由(软件)nrf中断处理函数给出
	nRF24_SendResult = xQueueCreate(1,1);			//创建nrf发送结果消息队列
	boatGyroscope_occFlag = xSemaphoreCreateMutex();	//创建船只姿态数据占用标志(互斥信号量)
	//建立遥控任务
    xTaskCreate(
		RemoteControl_Task,
		"RC task",
		512,
		(void*)&SendFre,
		11,
		&RemoteControl_TaskHandle
	);
	//建立摇杆值测量任务
	xTaskCreate(
		Rocker_Task,
		"RK",
		32,
		(void*)&RockerFre,
		8,
		&Rocker_TaskHandle
	);
	//建立nrf中断处理任务
	xTaskCreate(
		nRF24L01_Intterrupt_Task,
		"NI task",
		72,
		NULL,
		13,
		&nRF24L01_Intterrupt_TaskHandle
	);
	//建立键盘扫描任务
	xTaskCreate(
		KeyInput_Task,
		"key task",
		64,
		&Key_Fre,
		8,
		&KeyInput_TaskHandle
	);
	xTaskCreate(
		HMI_UpData,
		"HMI task",
		64,
		&HMI_Fre,
		13,
		&HMI_UpDataHandle
	);
	#if 1
	//建立串口反馈任务 -> 串口1
	xTaskCreate(
		User_FeedBack_Task,
		"UFB task",
		64,
		NULL,
		12,
		&User_FeedBack_TaskHandle
	);
	#endif
	//建立串口屏任务 -> 串口2
	xTaskCreate(
		HMI_Task,
		"HMI task",
		256,
		&HMI_Fre,
		9,
		&HMI_TaskHandle
	);
	HMI_ClearMsg();
	HMI_Msg("系统成功启动");
	USART_Clear(1);
	USART_Clear(2);
    vTaskDelete(NULL);
}

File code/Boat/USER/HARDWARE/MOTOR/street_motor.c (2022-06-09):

#include "street_motor.h"

#define PWM_Out_Port(Channel,Width)     PWM_Out(Channel,Width)  //PWM输出
#define PWM_Out_Read_Port(Channel)      PWM_Read(Channel)       //查看当前PWM输出

void StreetMotor_Set(streetMotor_Type*motor,float angle)
{
    if(angle>0 && angle<180)
    {
        if(motor->dir)
            PWM_Out_Port(motor->pwm_ch,180 - AngleToWidth(angle));
        else
            PWM_Out_Port(motor->pwm_ch,AngleToWidth(angle));
    }
}

void StreetMotor_SetWidth(streetMotor_Type*motor,uint16_t width)
{
    if(width>499 && width<2501)
    {
        PWM_Out_Port(motor->pwm_ch,width);
    }
}

unsigned int AngleToWidth(float angle)
{
    unsigned int temp;
    temp = (int)(11.111f*angle);
    temp += 500;
    return temp;
}

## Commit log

2022-01-11 nRF24L01 Add CurrentCfg,InterruptHandle wait code
2022-01-16 stm32f103ze nRF24L01 Pass
2022-01-18 nRF24L01 中断有问题
2022-01-18 nRF24L01中断触发正常,中断处理还未完成
2022-01-19 nRF24L01 中断处理函数(待写)
2022-01-20 nRF24L01 收发测试代码 nRF24L01 Sbuffer 操作代码
2022-01-22 nRF24L01 不能进入接收中断(可能没有接收到数据)
2022-01-28 整理了一下代码,FreeRTOS_Config.h还未配置
2022-01-30 nRF24的写多字节寄存器函数重写,freeRTOS验证通过
2022-02-02 对nrf24的中断处理方式做了一些改动
2022-02-07 加入了pwm相关代码(未测试)
2022-02-07 pwm测试通过(50Hz 1/20000s脉宽步进)
2022-02-14 nrf24的中断函数改为使用RTOS的二值信号量触发
2022-02-16 nrf24在RTOS下触发中断处理函数正常(未应答中断)
2022-02-17 对OS下的nrf24控制任务加入等待发送结果和等待接收从机软件回复代码(未测试)
2022-02-17 对RemoteControl_Task()接收从机回复bug的修复
2022-02-18 对nrf24发送中断软件处理函数加入了消息发送代码
2022-02-19 50Hz通讯频率相互通讯测试完成(从机没有使用软件回复)
2022-02-20 调整了任务栈大小,优化了RCtask,加入了栈水位检测
2022-02-22 对nrf24的接收缓存加入了配置功能(未验证)
2022-02-26 新建船板字子的代码工程
2022-02-26 移植了RTOS到Boat,nrf24还没完成移植
2022-03-04 boat PWM NRF OLED 测试通过
2022-03-06 mpu6050姿态结算 vofa 文件目录重组
2022-03-06 电调测试(开发板)通过
2022-03-06 代码计时测量 姿态解算 2.63ms
2022-03-09 移植RTOS进入船核心板子(未验证),遥控器也改了一点点(未测试)
2022-03-10 RTOS下通讯 2%丢包
2022-03-10 解决了船核心板中途复位死机bug(触发了外部中断),发现了主控板中途复位丢失信号bug
2022-03-10 远距离丢包严重,有的时候上电会丢失信号
2022-03-11 软件0%丢包,解决了上电丢信号的问题(超时重置nrf)
2022-03-11 mpu RTOS下长久运行
2022-03-11 nrf 80Hz 姿态传输有点卡顿
2022-03-11 50Hz通讯频率 160Hz陀螺仪刷新频率 20分钟稳定性测速通过
2022-03-12 增加了nrf重启函数,100hz陀螺仪频率,vofa波形图流畅,增加bsp_key(未测试)
2022-03-12 完成了bsp_key(待测试),增加了互斥信号量
2022-03-13 key通过,nrf有无法复现的死机bug
2022-03-13 nrf死机的bug:发出了ISRFlag信号量,但是IntTask没有执行
2022-03-16 T4C1无法输出高电平,其它还未测试
2022-03-16 更改了oled显示的方式(完全由oledTask操控oled函数),增加了系统状态,减小了任务堆栈分配
2022-03-17 单个无刷电调测试通过
2022-03-17 多电调控制任务单控制输出通过
2022-03-18 直流电机(待写)
2022-03-18 直流电机通过
2022-03-19 a4950分离,测试通过
2022-03-19 street_motor.c/.h 测试通过
2022-03-20 多器件抽象,hardware_def.h(测试通过),增加了部分通讯协议(未测试),串口屏无法调用(未知),摇杆测试(通过)
2022-03-20 摇杆值转化完成,RemoteCode增加了互斥锁(测试通过),摇杆值发送有点问题
2022-03-21 通讯协议摇杆数组传输正常,成功驱动电调和舵机
2022-03-21 Boat新增Main_Task()测试通过,主电调差速测试通过
2022-03-23 航模摇杆校准,测试通过
2022-03-25 HMI 消息框模块测试通过(基于串口1,裸机)
2022-03-31 串口屏幕自动下拉bug解决
2022-04-08 给Boat增加了部分注释,防止以后看不懂QAQ
2022-04-09 电池电压检测通过,暂时没有电池电压的nrf反馈
2022-04-09 初始化阶段nrf错误重启代码
2022-04-10 初始化阶段nrf重启代码通过
2022-04-13 HMI_Usart 主副油门数值更新验证通过
2022-04-17 实机HMI_Usart 主副油门验证通过,RemoteControl新增Main_Task
2022-04-20 船只增加相应遥控器直流电机命令代码,待测试
2022-04-21 串口屏幕信号栏测试通过 直流电机未测试(需要增加串口状态开关相应)
2022-04-22 信号测试注意:swd会影响nrf的信号! 现50Hz 95% 串口屏float测试通过
2022-04-23 Boat去除MainTask,使用portable包反馈,测试通过
2022-04-24 Boat\SOFTWARE\user_fun验证通过,增加并且移植了bsp_iic,带测试
2022-04-25 i2c分离测试,串口测试(状态开关未测)通过,等待写入串口读取
2022-04-26 HMI信号解析通过,更新了self_portable
2022-04-26 HMI控制直流电机通过,待优化
2022-04-26 Boat增加了其他由摇杆控制的硬件的代码,待测试
2022-04-27 舵机,直流电机,主电调(由遥控器控制) 测试通过
2022-04-28 整理了一下Boat代码的保函关系,增加了水位和pid的代码 待测试
2022-04-29 Boat增加了自动巡航代码(未完成)
2022-05-01 优化了程序结构,测试通过 增加了位置式pid 自动巡航节点 代码
2022-05-26 增加了各种电机的方向性定义(方便后期快速调整方向) 带测试
2022-05-30 串口屏程序中转下载测试通过,进入了临界区
2022-06-07 Boat oled dma刷新页面时发现字节倒置bug
2022-06-09 oled DMA循环刷新 串口屏中转升级 电机方向
2022-06-09 遥控器key、led驱动正常(还未绑定具体功能)
2022-06-09 水位传感器(压强式)驱动正常,缩放系数已校准
2022-06-11 气压计大气压归零函数，船只oled任务开关，通讯经常短链(可能是硬件问题)，遥控器LED信号反馈
2022-06-12 加入消息发送代码,其它功能测试后发现暂无影响,消息发送功能带测试
2022-06-14 直流电机控制bug解决(没加括号,运算优先级导致if语句判断错误)
2022-06-14 实际测试(硬件接口已经确定,各个电机方向确定,舵机角度对应确定)--舵机速度有一点点bug
2022-06-18 成功下水,舵机角度校准
2022-06-23 赛前第一次参数小修改各功能正常
2022-06-25 第一次结项总结
    [Remote_Core.SchDoc, 船核心板.SchDoc, 船驱动板.SchDoc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]
